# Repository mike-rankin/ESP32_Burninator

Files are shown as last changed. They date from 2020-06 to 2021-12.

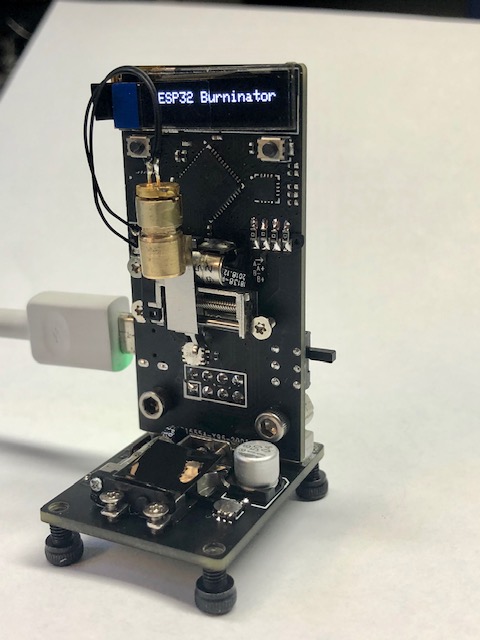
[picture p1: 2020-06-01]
Images/1.jpg

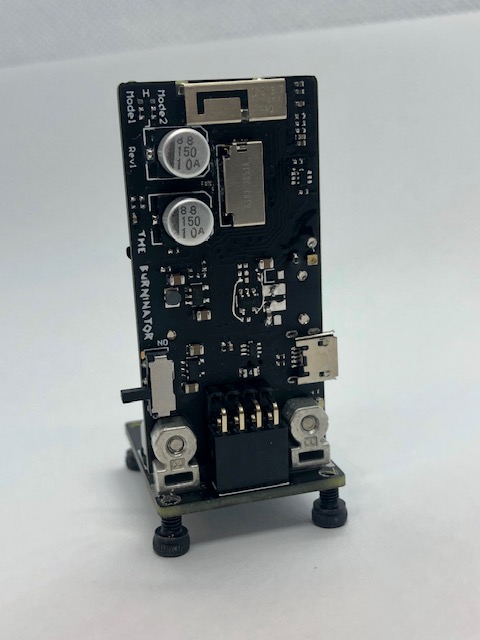
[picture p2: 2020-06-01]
Images/2.jpg

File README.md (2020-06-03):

# ESP32_Burninator
An ESP32 project using two linear stepper motors and a burning laser diode. I came up with the project name from being a longtime fan of the homestarrunnerdotcom videos. Please don't sue me.

The project started when I grabbed a few tiny linear stepper motors from Aliexpress [link](https://www.aliexpress.com/item/4000033935971.html?spm=a2g0s.9042311.0.0.27424c4dJ4Ao08) and wondered what I could do with them. They lack strength to cut material or draw using a pen but they should be able to hold dvd buring laser diode. A tiny adjustable lens from Aliexpress [link](https://www.aliexpress.com/item/4000328573867.html?spm=a2g0o.cart.0.0.258f3c00BAqm6e&mp=1) was needed used to focus the burn height. Pulling out the visible diode component and replacing it with the dvd diode was surprisingly easy.

A video of it in action: https://youtu.be/s-a9CgvyQM8





Top_Rev2_back

Top_Rev2_front

Bottom_Rev2_front

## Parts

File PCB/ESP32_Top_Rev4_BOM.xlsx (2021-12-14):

Designator | Quantity | Vendor | Description | Manufacturer | Value
ANT1 | 1 | Digi-Key | RF ANT 2.4GHZ STAMPED MET SLD | Proant AB | RF ANT 2.4GHZ STAMPED MET SLD
C1, C2, C4, C10, C22 | 5 | LCSC | CAP 0.1uF 16V 0402 | Yageo | 0.1uF
C3 | 1 | LCSC | CAP 1.5pF 0402 | Dafron | 1.5pF
C5, C6, C12 | 3 | LCSC | CAP 0.1uF 16V 0402 | Samsung | 1uF
C7, C8, C11, C16, C17, C18, C19 | 7 | LCSC | CAP 10uF 16V 0805 | Murata | 10uF
C9, C15 | 2 | LCSC | CAP 150uF, 10V SMT | Suncon | 150uF
C13 | 1 | LCSC | CAP 4.7uF 16V 0402 | Samsung | 4.7uF
C14 | 1 | LCSC | CAP 2.2uF 16V 0402 | Samsung | 2.2uF
C20 | 1 | LCSC | CAP 22nF 16V 0402 | Samsung | 22nF
D1 | 1 | LCSC | LED Green 0603 | Orient | Green
F1 | 1 | LCSC | 6V 1A 100ms 0805 PTC Resettable Fuse | TLC | 1A Fuse
H1 | 1 | LCSC | CONN HEADER 4X2 POS .100" RA | MINTRON | Male 4X2
J1 | 1 | Digi-Key | 9 (8 + 1) microSD SMT, Right Angle | Molex | MicroSD
J2 | 1 | LCSC | CONN RECPT MICRO USB | XKB | Micro USB
L1 | 1 | LCSC | Inductor 2.2uH 1.45A 2.0 x 2.0mm | Taiyo Yuden | 2.2uH
M1 | 1 | Aliexpress | MTR,LINEAR,SMT |  | Linear Motor
Q1 | 1 | LCSC | TRANS 2NPN 44V 0.1A SC-70-6 | Changjiang | BC847S
R1, R2, R3, R4, R11, R21 | 6 | LCSC | RES 0R 0402 | Uniroyal | 0R
R5, R7, R13, R15, R17, R18, R19, R23, R24, R28, R32, R34 | 12 | LCSC | RES 10K 0402 | Uniroyal | 10K
R6 | 1 | LCSC | RES 22.1K 0402 | Uniroyal | 22.1K
R8, R9 | 2 | LCSC | RES 2K 0402 | Uniroyal | 2K
R10 | 1 | LCSC | RES 390K 0402 | Uniroyal | 390K
R12 | 1 | LCSC | RES 47K 0402 | Uniroyal | 47K
R14 | 1 | LCSC | RES 100K 0402 | Uniroyal | 100K
R16 | 1 | LCSC | RES 49.9K 0402 | Uniroyal | 49.9K
R20 | 1 | LCSC | RES 90.9K 0402 | Uniroyal | 90.9K
R22 | 1 | LCSC | RES 4.99K 0402 | Uniroyal | 4.99K
R27 | 1 | LCSC | RES 1K 0402 | Uniroyal | 1K
R29, R30 | 2 | LCSC | RES 0.2R 0402 | Uniroyal | 0.2R
R33 | 1 | LCSC | RES 470R 0402 | Uniroyal | 470R
R35, R36 | 2 | LCSC | RES 22R 0402 | Uniroyal | 22R
S1 | 1 | LCSC | Toggle Switch Thu Hole | XKB | Toggle Switch
S2, S4 | 2 | LCSC | Switch SMD,3x4x2.5mm | Xunpu | Pushbutton
S3 | 1 | LCSC | SWITCH DETECT, DUAL, SMD,R/A | Alps | Limit Switch
U1 | 1 | LCSC | IC BRIDGE USB TO UART 24QFN | Silicon Labs | CP2104N
U2 | 1 | LCSC | WIFI/Bluetooth, QFN-48 7x7 | Espressif | ESP32-PICO-D4
U3, U6 | 2 | LCSC | IC LDO 3.3V 0.5A SOT23-5 | Holtek | HT7833
U4 | 1 | LCSC | IC DC SWITCHING REG 1A SOT23-5 | Richtek | Step Down
U5 | 1 | Digi-Key | IC STEPPER MOTOR DRIVER 16-VFQFPN(3x3) | ST Micro
U7 | 1 | LCSC | TVS 5V SOT-363 | Yenji | ESD
X1 | 1 | Buy-Display | 96x16 OLED_GLASS

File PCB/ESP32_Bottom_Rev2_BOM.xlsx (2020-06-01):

Designator | Quantity | Vendor | Description | Manufacturer | Value | Part_Number
C1 | 1 | LCSC | CAP 150uF, 10V SMT | Suncon | 150uF | C242018
C2 | 1 | LCSC | CAP 22nF 16V 0402 | Samsung | 22nF | C318579
H1 | 1 | LCSC | CONN REPT 4X2 POS .100" RA | CONNFLY | Female 4X2 | C92271
M1 | 1 | Aliexpress | MTR,LINEAR,SMT |  | Linear Motor | shorturl.at/cQ269
R1, R3, R9, R12, R13 | 5 | LCSC | RES 10K 0402 | Uniroyal | 10K | C25744
R2 | 1 | LCSC | RES 47K 0402 | Uniroyal | 47K | C25792
R4 | 1 | LCSC | RES 90.9K 0402 | Uniroyal | 90.9K | C26989
R5 | 1 | LCSC | RES 4.99K 0402 | Uniroyal | 4.99K | C25903
R6, R7 | 2 | LCSC | RES 0.2R 0402 | Uniroyal | 0.2R | C270629
R8 | 1 | LCSC | RES 1K 0402 | Uniroyal | 1K | C11702
S1 | 1 | LCSC | SWITCH DETECT, DUAL, SMD,R/A | Alps | Limit Switch | C231760
ST1, ST2 | 2 | pemnet.com | STANDOFF PCB RA 440 SMT | PENN | RA Mount | SMTRA440-9-6ET
U1 | 1 | Digi-Key | IC STEPPER MOTOR DRIVER 16-VFQFPN(3x3) | ST Micro |  | STSPIN220

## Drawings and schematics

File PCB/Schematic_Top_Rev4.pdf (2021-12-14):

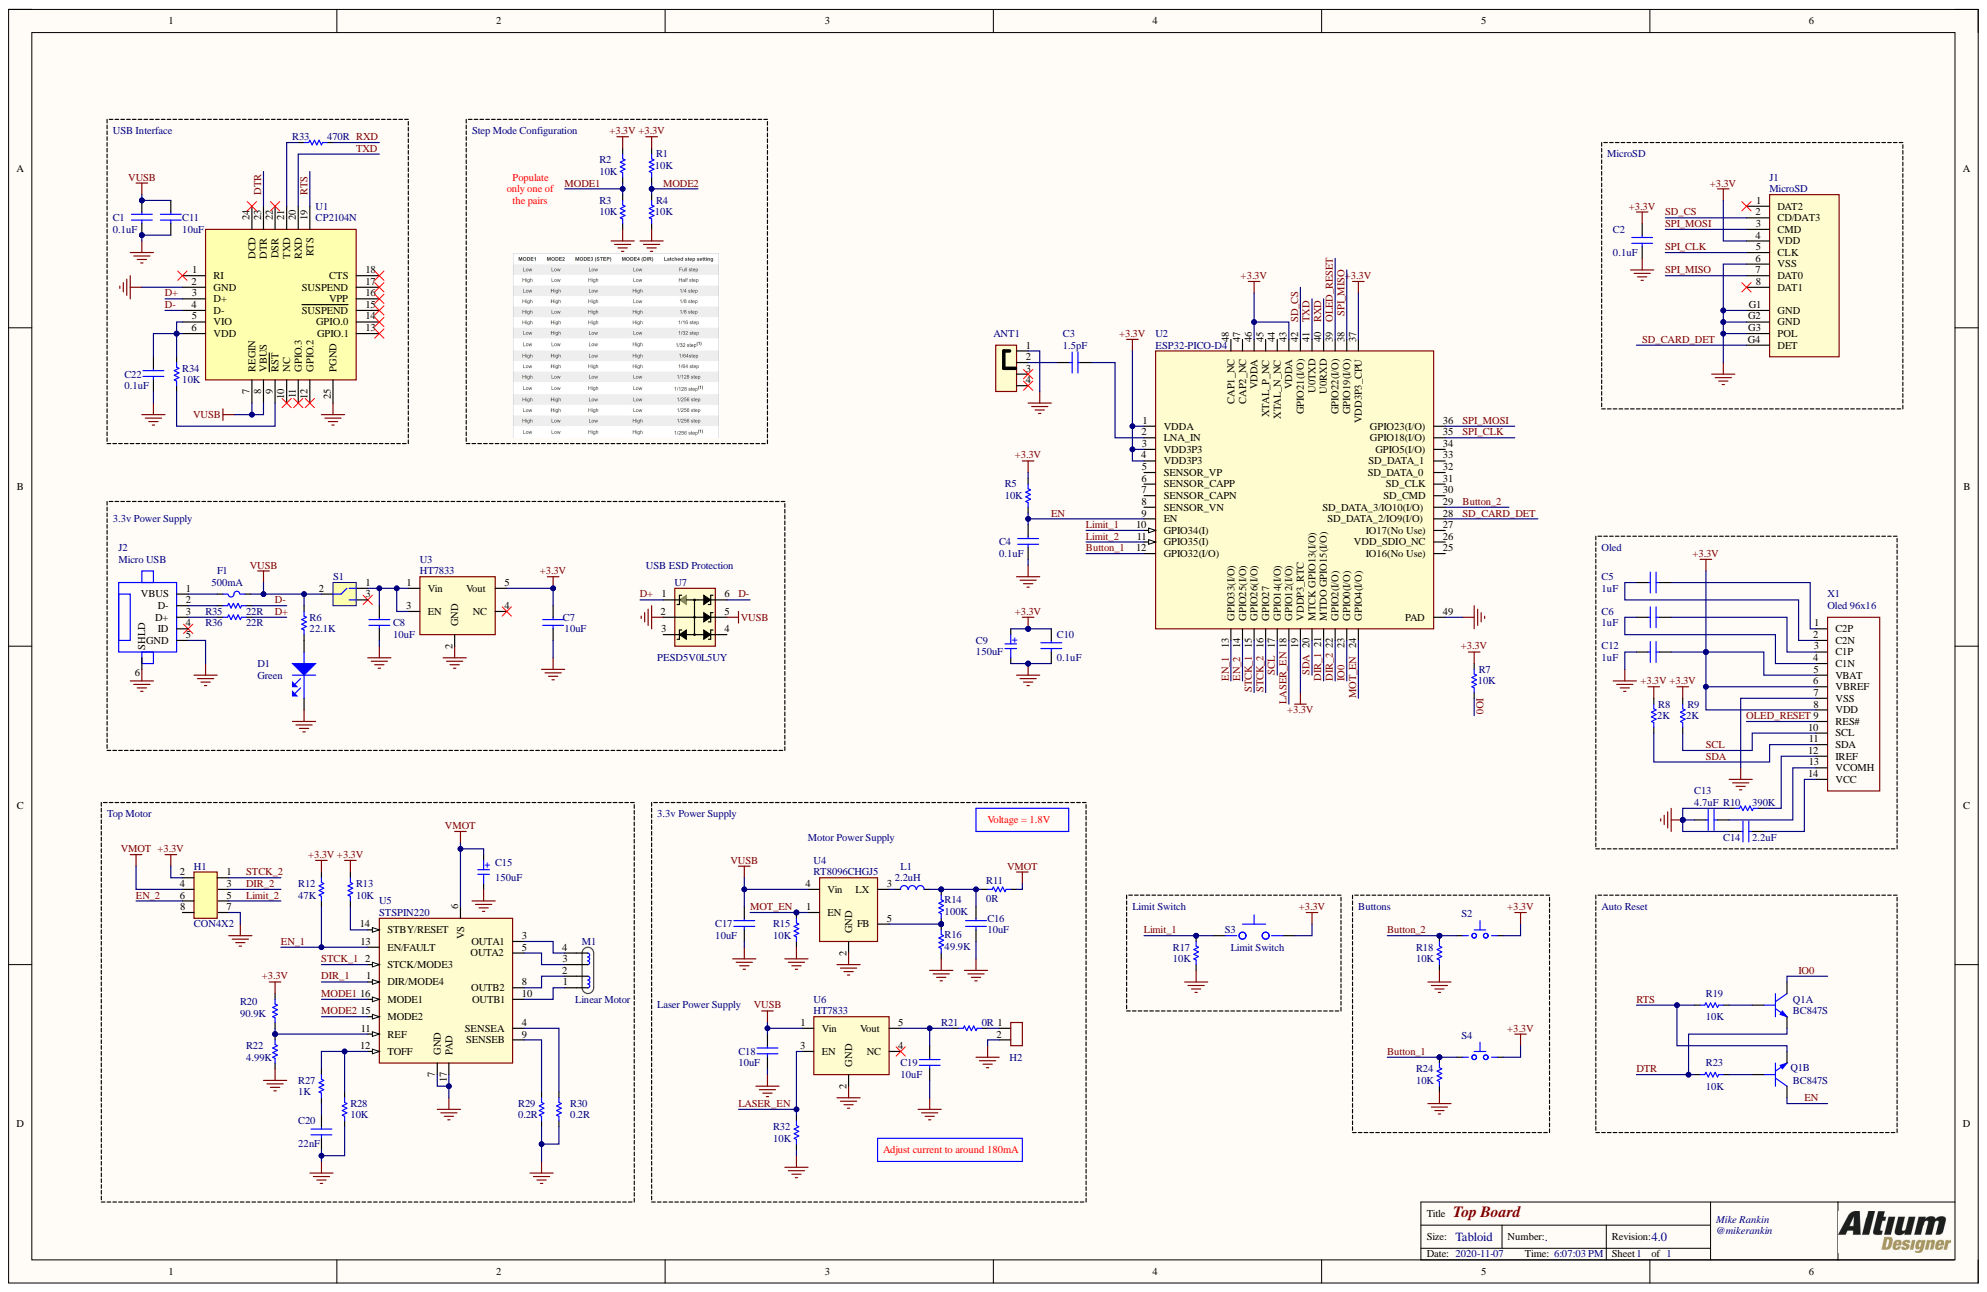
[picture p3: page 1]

RTS 19 RXD 20 TXD 21 DSR 22 DTR 23

1 1 | 1

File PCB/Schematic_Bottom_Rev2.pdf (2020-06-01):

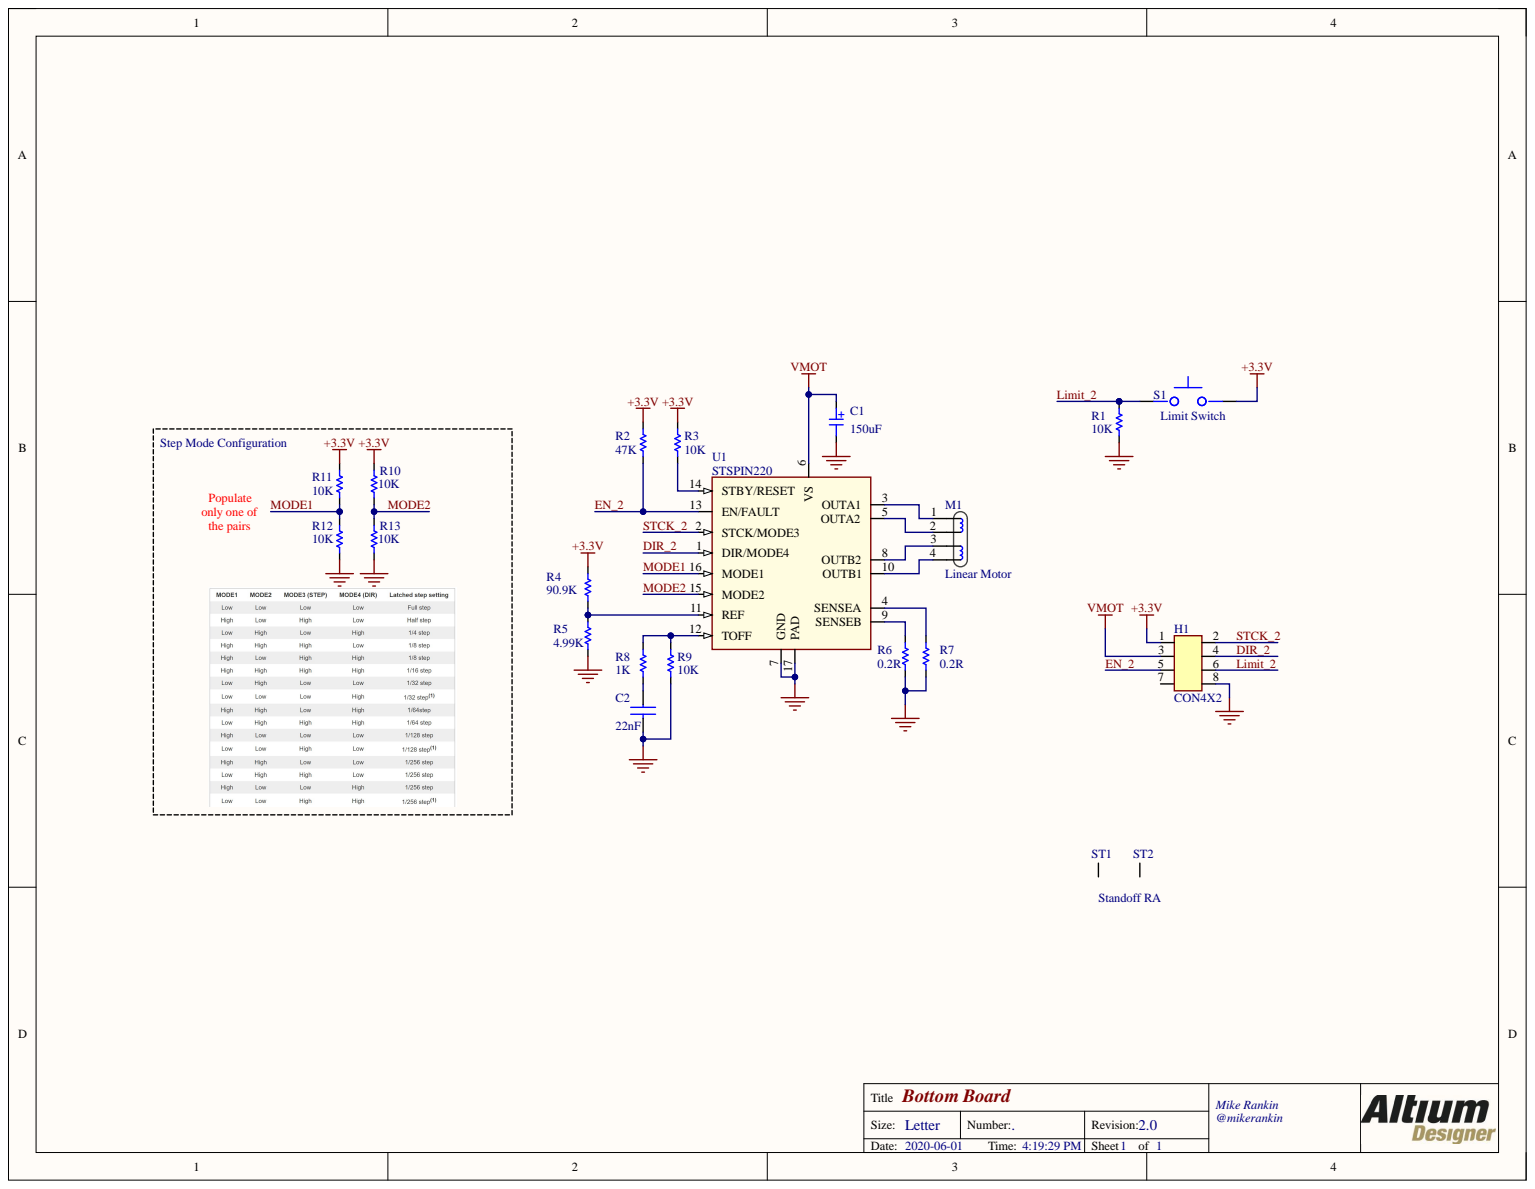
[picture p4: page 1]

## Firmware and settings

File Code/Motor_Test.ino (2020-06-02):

//ESP32 Dev Board

#include <Wire.h>
#include <Adafruit_GFX.h>
#include <Adafruit_SSD1306.h>

#define MOT_EN 4    //Enable Power to Top motor power supply 
#define LASER_EN 12 //Enable Power to laser
#define RIGHT_PUSHBUTTON 10   
#define LEFT_PUSHBUTTON 32 

int RIGHT_BUTTON = 0;  //Right PushButton
int LEFT_BUTTON = 0;   //Left PushButton

int i=0;

int TOP_LIMIT = 0;
int BOTTOM_LIMIT = 0;

Adafruit_SSD1306 display(96, 16, &Wire, 22);

//Top Motor
#define EN_1 33           //Motor Enable
#define STCK_1 26         //Motor Clock
#define DIR_1 15          //Motor Direction
#define LIMIT_SWITCH_1 34 //Top Limit Switch

//Bottom Motor
#define EN_2 25           //Motor Enable
#define STCK_2 27         //Motor Clock
#define DIR_2 2           //Motor Direction
#define LIMIT_SWITCH_2 35 //Bottom Limit Switch


void setup() 
{
 Serial.begin(9600);
 Wire.begin(13, 14); 
 display.setRotation(2);
 display.begin(SSD1306_SWITCHCAPVCC, 0x3C);

 display.display();
 delay(500); 
 display.clearDisplay();
 display.setTextSize(1);             // Normal 1:1 pixel scale
 display.setTextColor(WHITE);        // Draw white text
 display.setCursor(0,0);             // Start at top-left corner
 display.println(F("ESP32 Burninator"));
 display.display();
 delay(2000);

 pinMode(RIGHT_PUSHBUTTON, INPUT);
 pinMode(LEFT_PUSHBUTTON, INPUT); 
 
 pinMode(LIMIT_SWITCH_2, INPUT); //Bottom 
 pinMode(LIMIT_SWITCH_1, INPUT); //Top
 
 pinMode(MOT_EN,     OUTPUT);
 pinMode(LASER_EN,   OUTPUT);
 pinMode(EN_1,       OUTPUT);   
 pinMode(EN_2,       OUTPUT);
 pinMode(STCK_1,     OUTPUT); 
 pinMode(STCK_2,     OUTPUT);
 pinMode(DIR_1,      OUTPUT); 
 pinMode(DIR_2,      OUTPUT); 

 digitalWrite(MOT_EN, HIGH); //Power up Motors
 delay(100);
 
 digitalWrite(EN_1, HIGH); //Enable Motor
 digitalWrite(EN_2, HIGH); //Enable Motor

  Go_To_Center();
  Burn_Square();

}


void loop() 
{
 digitalWrite(EN_1, HIGH); //Enable Motor
 digitalWrite(EN_2, HIGH); //Enable Motor
  
 RIGHT_BUTTON = digitalRead(RIGHT_PUSHBUTTON); //read the right button
 LEFT_BUTTON = digitalRead(LEFT_PUSHBUTTON);   //read the left button

 digitalWrite(LASER_EN, LOW); //Power off Laser
}

void Move_Top_Motor_Right()
{
 digitalWrite(DIR_1, HIGH); //Direction: LOW=Left, HIGH=Right 

 for (int i=0; i <= 10; i++)  //Move left
  {
   digitalWrite(STCK_1, HIGH);
   delay(1);
   digitalWrite(STCK_1, LOW);
   delay(1);
  }
}

void Move_Top_Motor_Left()
{
 digitalWrite(DIR_1, LOW); //Direction: LOW=Left, HIGH=Right  

 for (int i=0; i <= 10; i++)  //Move left
  {
   digitalWrite(STCK_1, HIGH);
   delay(1);
   digitalWrite(STCK_1, LOW);
   delay(1);
  }
}

void Move_Bottom_Motor_Out()
{
 digitalWrite(EN_2, HIGH);  //Enable Bottom Motor
 digitalWrite(DIR_2, HIGH); //Direction: LOW=Out, HIGH=In 

 for (int i=0; i <= 10; i++)  //Move left
  {
   digitalWrite(STCK_2, HIGH);
   delay(1);
   digitalWrite(STCK_2, LOW);
   delay(1);
  }
}

void Move_Bottom_Motor_In()
{
 digitalWrite(EN_2, HIGH);  //Enable Bottom Motor
 digitalWrite(DIR_2, LOW); //Direction: LOW=Out, HIGH=In 

 for (int i=0; i <= 10; i++)  //Move left
  {
   digitalWrite(STCK_2, HIGH);
   delay(1);
   digitalWrite(STCK_2, LOW);
   delay(1);
  }
}


void Go_To_Center()
{  
 for (int j=0; j<=150; j++)
 {
  Move_Top_Motor_Right();
  j=j+1;
  display.clearDisplay();
  display.setCursor(10,0);
  display.print("X: ");            
  display.print(j);
  display.display();
 }
 
 for (int j=0; j<=150; j++)
 {
  Move_Top_Motor_Left();
  j=j+1;
  display.clearDisplay();
  display.setCursor(10,0); 
  display.print("-X: ");          
  display.print(j);
  display.display();
 }

 for (int j=0; j<=60; j++)
 {
  Move_Top_Motor_Right();
  j=j+1;
  display.clearDisplay();
  display.setCursor(10,0); 
  display.print("X: ");          
  display.print(j);
  display.display();
 }

 for (int k=0; k<=150; k++)
 {
  Move_Bottom_Motor_In();
  k=k+1;
  display.clearDisplay();
  display.setCursor(30,0);
  display.print("-Y: ");           
  display.print(k);
  display.display();
 }

 for (int k=0; k<=150; k++)
 {
  Move_Bottom_Motor_Out();
  k=k+1;
  display.clearDisplay();
  display.setCursor(30,0);
  display.print("Y: ");           
  display.print(k);
  display.display();
 }

 for (int k=0; k<=200; k++)
 {
  Move_Bottom_Motor_In();
  k=k+1;
  display.clearDisplay();
  display.setCursor(30,0); 
  display.print("-Y: ");          
  display.print(k);
  display.display();
 }
}

void Burn_Square()
{ 
 Laser_Enable();
 display.clearDisplay();
 display.setCursor(0,0);           
 display.print("Burninating!");
 display.display();
 
 for (int j=0; j<=20; j++)
 {
  Move_Top_Motor_Right();
  delay(100);
 }

 for (int j=0; j<=20; j++)
 {
  Move_Bottom_Motor_Out();
  delay(100);
 }

 for (int j=0; j<=20; j++)
 {
  Move_Top_Motor_Left();
  delay(100);
 }

 for (int j=0; j<=20; j++)
 {
  Move_Bottom_Motor_In();
  delay(100);

  display.clearDisplay();
  display.setCursor(0,0);           
  display.print("Done...");
  display.display();
 }

 digitalWrite(LASER_EN, LOW);
 
 for (int k=0; k<=150; k++)
 {
  Move_Bottom_Motor_Out();
 }
    
}

void Laser_Enable()
{
 digitalWrite(LASER_EN, HIGH); //Power up Laser
}

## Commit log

2020-06-01 Added PCB files
    [ESP32_Bottom_Rev2_BOM.xlsx, ESP32_Top_Rev2_BOM.xlsx]
2020-06-01 Updated bom
    [ESP32_Bottom_Rev2_BOM.xlsx, ESP32_Top_Rev2_BOM.xlsx]
2020-06-02 replaced .xls bom with .csv
    [ESP32_Bottom_Rev2_BOM.csv, ESP32_Bottom_Rev2_BOM.xlsx, ESP32_Top_Rev2_BOM.csv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]
2021-12-14 Updated files
    [ESP32_Bottom_Rev2_BOM.csv, ESP32_Bottom_Rev2_BOM.xlsx, ESP32_Top_Rev2_BOM.csv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]
